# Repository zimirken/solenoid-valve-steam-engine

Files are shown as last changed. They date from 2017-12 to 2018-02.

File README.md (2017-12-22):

# solenoid-valve-steam-engine
My latest steam engine using hall sensors and a solenoid valve.

This is for my solenoid valve steam engine using electronic controls. It uses an industrial air cylinder and valve. THERE IS NO MACHINING REQUIRED ANYWHERE! I see all these steam projects and you need a well equipped machine shop to produce anything big enough to do useful work, and I think that's dumb. So I set out to prove everyone wrong by building a complete steam powerplant that uses no machine tools beyond small hand tools (and a 3D printer), no welding (or brazing!), and no expensive specialty parts. Everything was bought from local hardware stores, ebay, aliexpress, amazon, etc. 

Even the boiler is easy to make, flare fittings, black pipe, and pop riveted sheet metal. I see too many "steam engines" that spend their whole lives running off an air compressor. This boiler is safe, compact, and powerful. It has no large heated pressure vessels to explode. In the event of a problem, the small copper tubing will rupture with a loud pop, some steam, and little danger. The boiler is an advanced design using a motor driven circulation pump that allows you to get maximum steam from minimum heated surface area, while still having simple controls. This advanced design actually makes it easier to build compared to more traditional designs.

My current powerplant has only one item that costs over ~$30, the burner. While this project will nickel and dime you to death, there are no big purchases that are hard to save up for. I know how hard it is to justify even a hundred dollars for a single item, and how easy it is to go broke five dollars at a time.

I want to thank china for making this possible and affordable. Their industrial air cylinder and valves actually work better with steam than the fancier brands. The cheap ones from china have little to no plastic parts, and seem to handle steam just fine. 

I previously tried to use a rotary encoder for valve timing, but I have now settled on using hall sensors and a magnet that moves with the cylinder. I added the rotary encoder code, and the cad files for the engine, but I do not recommend going this route.

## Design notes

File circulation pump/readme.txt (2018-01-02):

These are the latest designs for the circulation pump. Mine uses a clippard air cylinder from a junk bin and an electric gearmotor from ebay.
This pump pumps ~0.9cc/s, which is about right for my burner output. You want to aim for a circulation rate of around 5 times the evaporation rate.
Clippard CR-UDR-17-2 air cylinder
1" bore by 2" stroke.
TSINY TS-40CZ495-218 gear motor
12 volts, 35rpm, make sure you have enough torque to overcome the rod pressure and the friction.
Oh, and a 608 bearing and some metric bolts.

You can use something different, but you may have to edit the models. I got these off ebay.

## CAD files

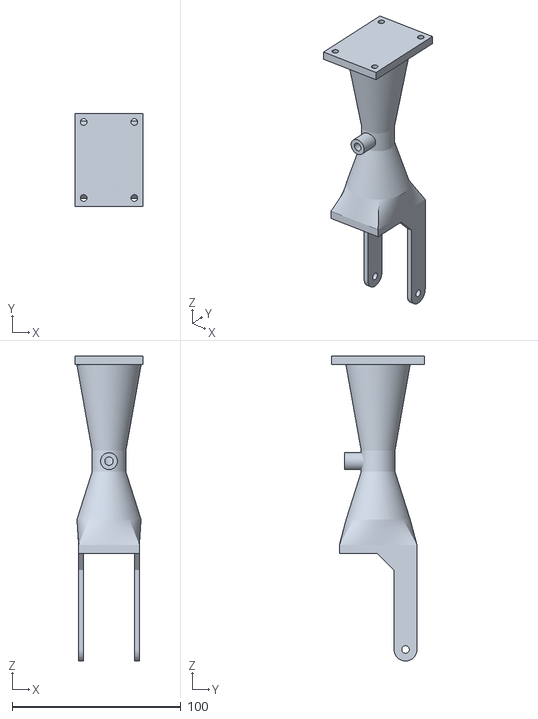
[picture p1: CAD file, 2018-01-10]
burner 2/venturi 1.stl
40.0 x 55.0 x 180.6

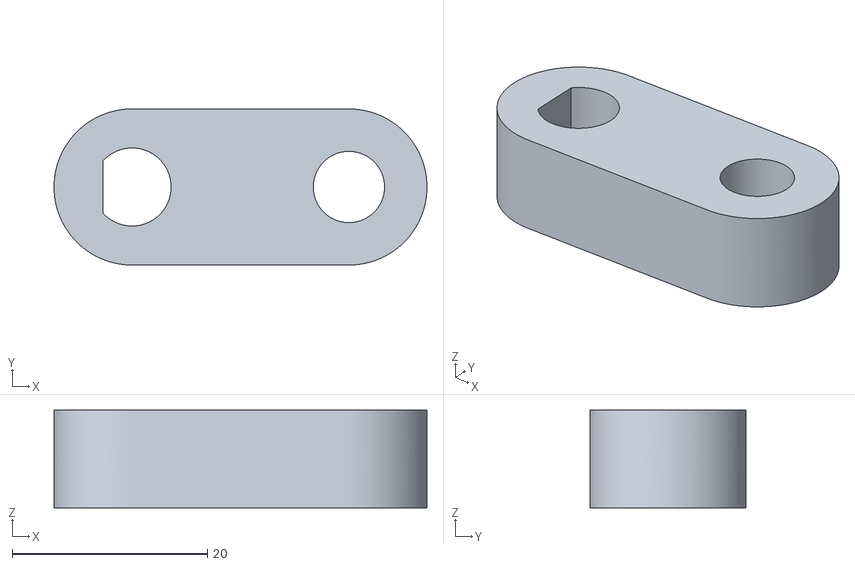
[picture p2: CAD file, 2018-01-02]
circulation pump/crank.stl
38.2 x 16.0 x 10.0

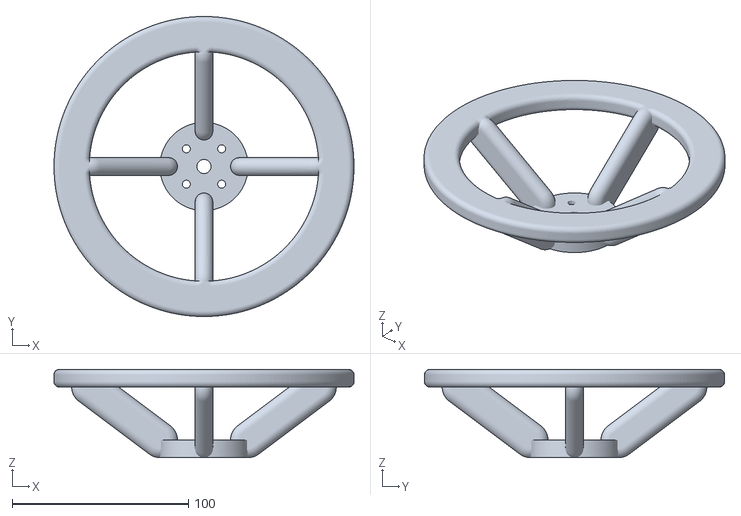
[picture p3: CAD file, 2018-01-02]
hydraulic steering/steering wheel/steering wheel.stl
170.0 x 170.0 x 50.0

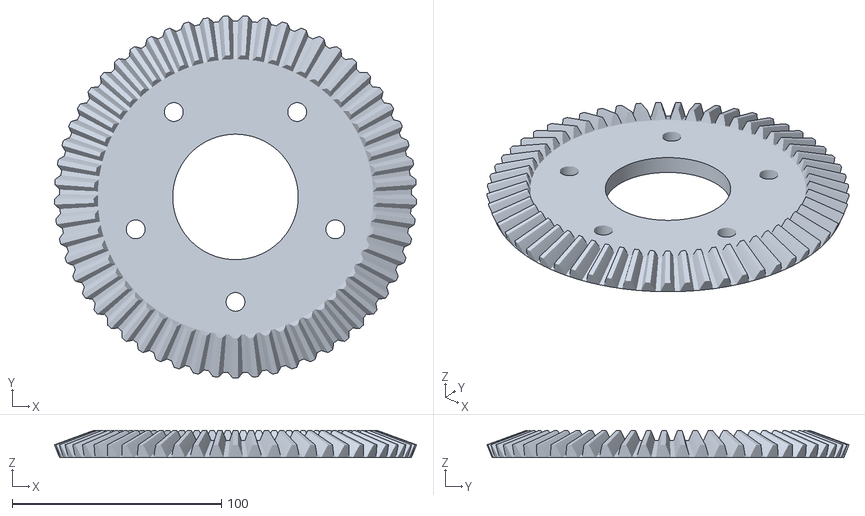
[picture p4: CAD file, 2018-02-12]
two cylinder shaft drive 2/engine/Design Accelerator/Bevel Gear21.stl
173.2 x 173.2 x 13.0

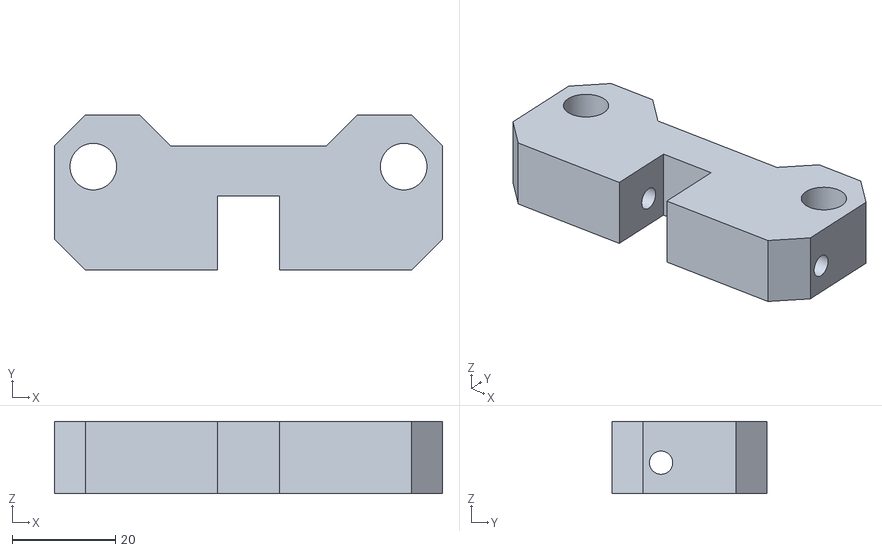
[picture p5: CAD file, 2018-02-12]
two cylinder shaft drive 2/sensor bracket.stl
75.0 x 30.0 x 14.0

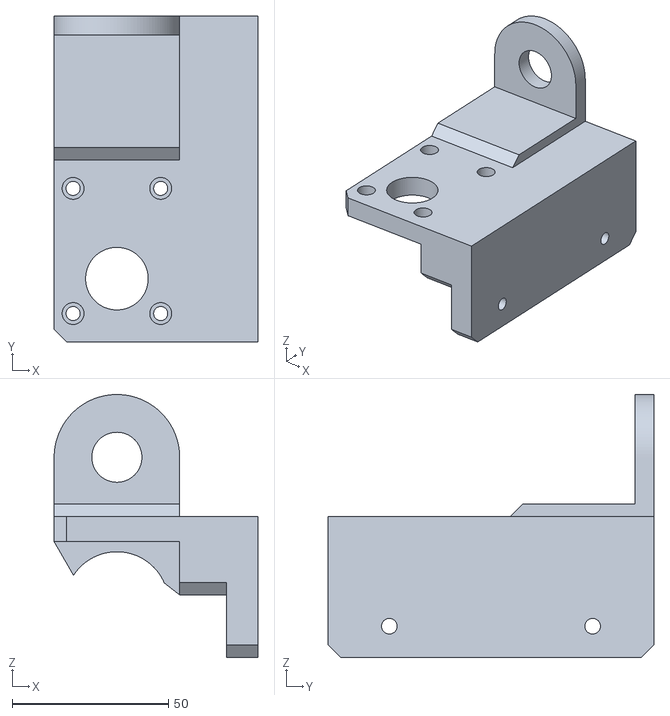
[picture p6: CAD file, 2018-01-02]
circulation pump/frame.stl
65.1 x 104.1 x 84.1

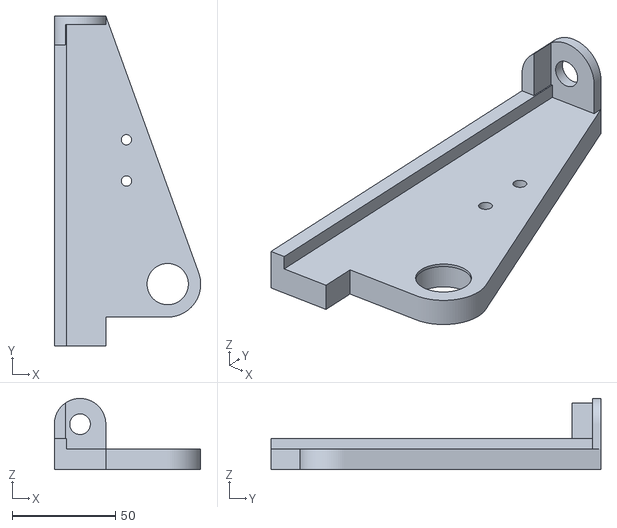
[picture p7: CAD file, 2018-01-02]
hydraulic steering/steering wheel/frame.stl
71.0 x 160.0 x 34.5

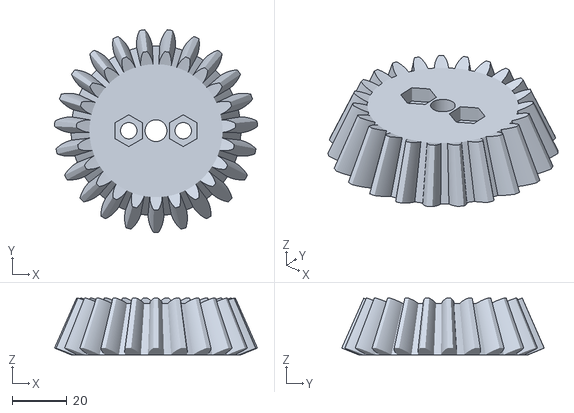
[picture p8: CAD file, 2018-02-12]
two cylinder shaft drive 2/engine/Design Accelerator/Bevel Gear11.stl
74.5 x 74.3 x 20.8

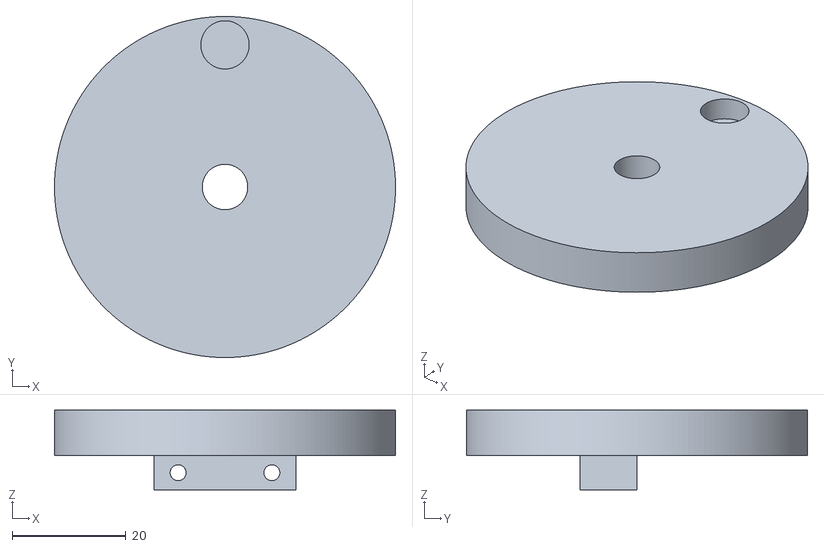
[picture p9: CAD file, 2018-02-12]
two cylinder shaft drive 2/sensor wheel.stl
60.0 x 60.0 x 14.0

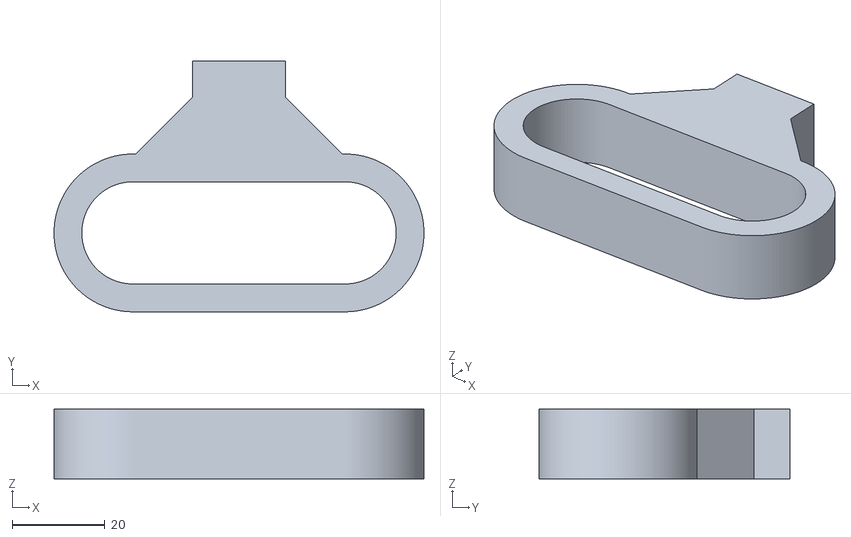
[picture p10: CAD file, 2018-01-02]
circulation pump/yoke.stl
79.7 x 54.0 x 15.0

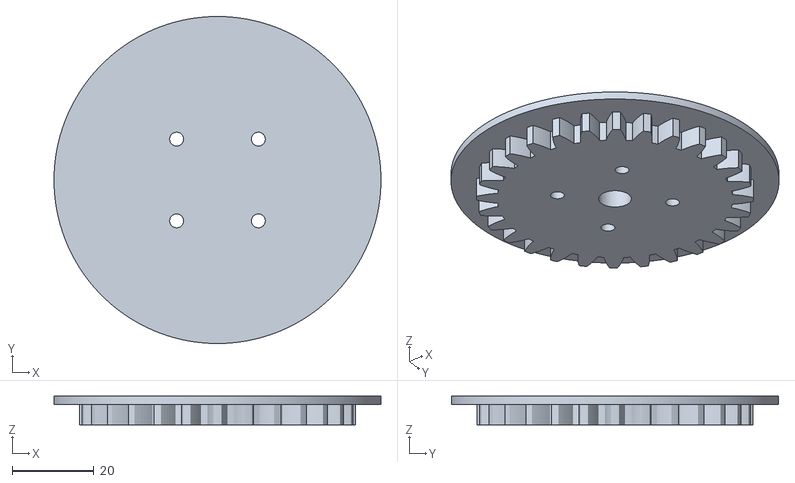
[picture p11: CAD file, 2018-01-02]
hydraulic steering/steering wheel/Spur Gear12.stl
80.0 x 80.0 x 7.00

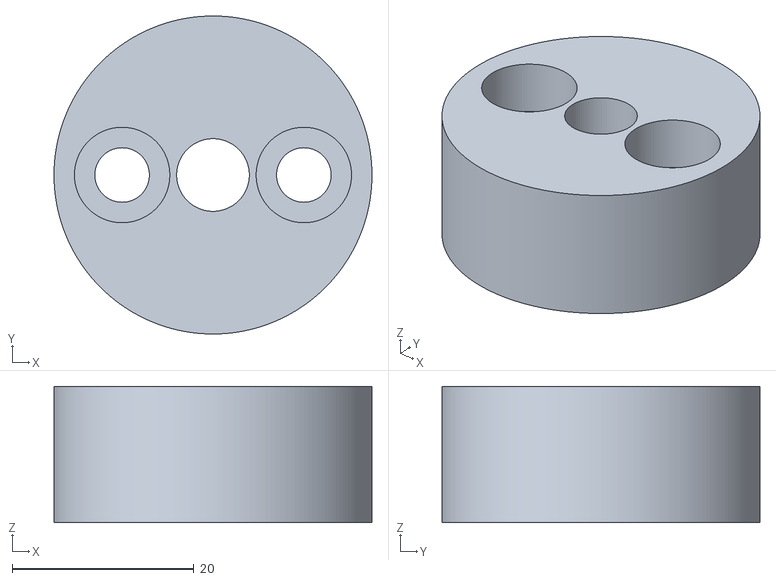
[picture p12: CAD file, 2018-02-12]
two cylinder shaft drive 2/gear thrust cup.stl
35.0 x 35.0 x 15.0

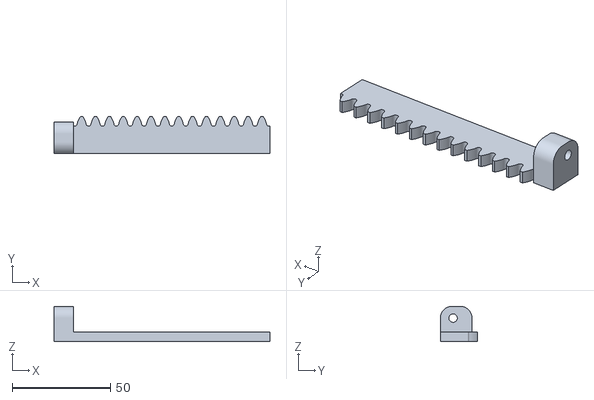
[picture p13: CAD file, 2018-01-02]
hydraulic steering/steering wheel/rack.stl
110.0 x 19.0 x 18.0

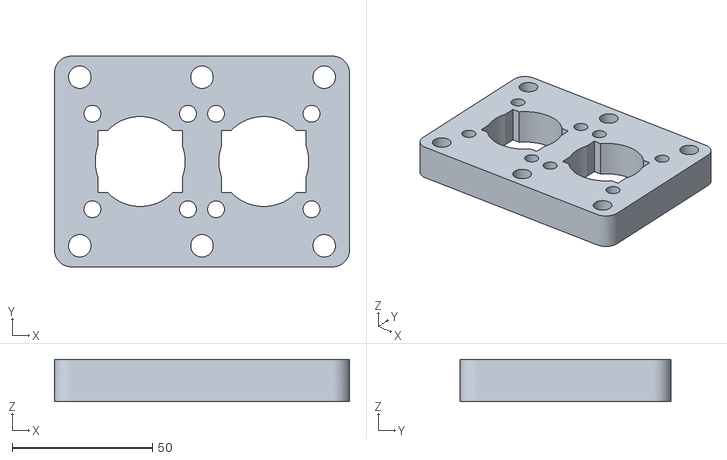
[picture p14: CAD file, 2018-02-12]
two cylinder shaft drive 2/cylinder frame.stl
105.0 x 75.0 x 15.0

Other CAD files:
two cylinder shaft drive 2/gear frame 1.stl
two cylinder shaft drive 2/con rod.stl
two cylinder shaft drive 2/crank web.stl
two cylinder shaft drive 2/shaft collar.stl
burner 2/OldVersions/venturi 1.0001.ipt
burner 2/venturi 1.ipt
circulation pump/OldVersions/circulation pump.0003.iam
circulation pump/OldVersions/crank.0001.ipt
circulation pump/OldVersions/frame.0003.ipt
circulation pump/OldVersions/yoke.0001.ipt
circulation pump/circulation pump.iam
circulation pump/crank.ipt
circulation pump/cylinder.ipt
circulation pump/frame.ipt
circulation pump/motor.ipt
circulation pump/yoke.ipt
hydraulic steering/CJ2B16-100Z.iam
hydraulic steering/CJ2B16-100Z.ipt
hydraulic steering/CJ2B16-100Z_1.ipt
hydraulic steering/CJ2B16-100Z_2.ipt
hydraulic steering/CJ2B16-100Z_3.ipt
hydraulic steering/CJ2B16-100Z_4.ipt
hydraulic steering/CJ2B16-100Z_5.ipt
hydraulic steering/CJ2B16-100Z_6.ipt
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

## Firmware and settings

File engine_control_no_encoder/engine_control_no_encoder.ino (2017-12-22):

/* This is the control program for a steam engine that uses a 5 port 3 position closed center solenoid valve to drive an industrial air cylinder.
 *  My previous engine designs used a rotary encoder, but this one will use a magnet attached to the piston rod that travels past a set of 4 hall sensors. 
 *  Two at TDC and BDC, and two that are in the middle that can be physically moved to control cutoff. This should make things waaaay simpler.
 */

//using the button parts of the automation library to simplify the cylinder position sensing
#include <Automaton.h>    


#include "Arduino.h"

#include <digitalWriteFast.h>  // library for high performance reads and writes by jrraines
                               // see http://www.arduino.cc/cgi-bin/yabb2/YaBB.pl?num=1267553811/0
                               // and http://code.google.com/p/digitalwritefast/
 


//disable debugging once everything works
//#define EnableDebug

#ifdef EnableDebug
unsigned long previousMillis = 0;  
const long interval = 1000;
#endif


static int TDCPin = 2;
static int BDCPin = 3;
static int TopCutoffPin = 4;
static int BottomCutoffPin = 5;
static int EngineEnablePin = 7;
static int Solenoid1Pin = 10;     //solenoid 1 controls top solenoid
static int Solenoid2Pin = 11;     //solenoid 2 controls bottom solenoid
static int AdvancePin = 6;




int CycleState = 1;
/*  
 *  1 = top cylinder admission
 *  2 = top cylinder expansion
 *  3 = bottom cylinder admission
 *  4 = bottom cylinder expansion
 */

int Advance = 0;
int EEnable = 0;



Atm_button TDC, BDC, TopCutoff, BottomCutoff;

void setup()
{
  #ifdef EnableDebug
  Serial.begin(115200);
  #endif
 
 
  
  pinMode(EngineEnablePin, INPUT_PULLUP);
  pinMode(AdvancePin, INPUT_PULLUP);

  TDC.begin(TDCPin)
    .debounce(0)
    .onPress(TDC_Press)
    .onRelease(TDC_Release);

  BDC.begin(BDCPin)
    .debounce(0)
    .onPress(BDC_Press)
    .onRelease(BDC_Release);

  TopCutoff.begin(TopCutoffPin)
    .debounce(0)
    .onPress(TopCutoff_Press)
    .onRelease(TopCutoff_Release);

  BottomCutoff.begin(BottomCutoffPin)
    .debounce(0)
    .onPress(BottomCutoff_Press)
    .onRelease(BottomCutoff_Release);

  pinMode(Solenoid1Pin, OUTPUT);    
  pinMode(Solenoid2Pin, OUTPUT);    

  

}
 
void loop()
{
  //this loop includes no delays or anything, should execute as fast as reasonable


   //read switch states
   Advance = digitalReadFast(AdvancePin);
   EEnable = digitalReadFast(EngineEnablePin);


   //state program
   automaton.run();
   
   
   //all the valve control is handled in this sub
   SolenoidControl();


   
   #ifdef EnableDebug

   unsigned long currentMillis = millis();

   if (currentMillis - previousMillis >= interval) {
    // save the last time you blinked the LED
    previousMillis = currentMillis;
    Serial.print("Advance Pin:");
    Serial.println(Advance);
    Serial.print("State:");
    Serial.println(CycleState);
   }
   #endif
   
   
   
}

//when advance is enabled, the cylinder states change on rising. When advance is disabled, cylinder states change on falling.
void TDC_Press(int idx, int v, int up) {
  if (Advance == 0) {
    CycleState = 1;
  }
}

void TopCutoff_Press(int idx, int v, int up) {
  if (Advance == 0) {
    if (CycleState == 1) {
      CycleState = 2;
    }
  }
}

void BDC_Press(int idx, int v, int up) {
  if (Advance == 0) {
    CycleState = 3;
  }
}

void BottomCutoff_Press(int idx, int v, int up) {
  if (Advance == 0) {
    if (CycleState == 3) {
      CycleState = 4;
    }
  }
}

//advance disabled
void TDC_Release(int idx, int v, int up) {
  if (Advance == 1) {
    CycleState = 1;
  }
}

void TopCutoff_Release(int idx, int v, int up) {
  if (Advance == 1) {
    if (CycleState == 1) {
      CycleState = 2;
    }
  }
}

void BDC_Release(int idx, int v, int up) {
  if (Advance == 1) {
    CycleState = 3;
  }
}

void BottomCutoff_Release(int idx, int v, int up) {
  if (Advance == 1) {
    if (CycleState == 3) {
      CycleState = 4;
    }
  }
}



//here is the important part.
 
void SolenoidControl() {

  //disable the engine if the engine enable switch is off
  if (EEnable == 1) {
    digitalWriteFast(Solenoid1Pin, LOW);
    digitalWriteFast(Solenoid2Pin, LOW);
    return;
  }


  //top admission
  if (CycleState == 1) {
    digitalWriteFast(Solenoid1Pin, HIGH);
    digitalWriteFast(Solenoid2Pin, LOW);
  }
  //top expansion
  if (CycleState == 2) {
    digitalWriteFast(Solenoid1Pin, LOW);
    digitalWriteFast(Solenoid2Pin, LOW);
  }
  //bottom admission
  if (CycleState == 3) {
    digitalWriteFast(Solenoid1Pin, LOW);
    digitalWriteFast(Solenoid2Pin, HIGH);
  }
  //bottom expansion
  if (CycleState == 4) {
    digitalWriteFast(Solenoid1Pin, LOW);
    digitalWriteFast(Solenoid2Pin, LOW);
  }  
  
}
  
  
  
  
  
  
  
